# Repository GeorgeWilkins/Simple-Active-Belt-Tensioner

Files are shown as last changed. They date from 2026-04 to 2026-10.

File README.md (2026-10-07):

> 📢 **Important:** This is a _pre-release_ of the project and considered to be under active development and testing. If you're not prepared to do some tinkering and/or deal with initial usability issues, it is recommended that you do not attempt to build it right now and instead wait for the `v1.0` release

> 📰 **Latest News:** We now have a [Discord Server](https://discord.gg/YwW3TvEJEv) for pre-build questions, troubleshooting and technical support. You can also share details and photos of your build there!

SABT Logo

Diagram

# Simple Active Belt Tensioner

A haptic device for sim racing, designed specifically for people who do not have a background in software or electronics.

It requires **no soldering or programming** and can be built for **as little as ~215 GBP** _including the harness_.

## What Is It?

Introduction Video (https://youtu.be/b3R1tQvu-o4)

An _active belt tensioner_ is a device that attaches between your sim rig and the anchor points of your racing harness. It dynamically tensions the harness in response to game telemetry; giving a sense of the forces you'd be experencing in a vehicle when changing speed, braking, cornering and jumping/landing.

It works with **any game fully supported by [SimHub](https://www.simhubdash.com/)**, but the current software is designed primarily for racing games and simulators.

This project consists of three parts:
- A shopping list of [components](#what-does-it-cost), readily available from online sellers
- Printable [parts](/Printables/) and instructions on how to assemble them
- A _SimHub_ plugin that controls the hardware and allows customisation of the effects

The printable files and software are **completely free** (except the required [SimHub License](https://www.simhubdash.com/get-a-license/)). The printed part designs are `CERN-OHL-P` licensed (open-source), and the software is `MIT` licensed, which essentially means you can do what you like with either; including selling printed/machined parts kits.

### Design Goals
- Lowest Practical Cost
- Minimal Parts & Tools
- No Soldering
- No Programming
- No 'Reclaimed' Parts
- Direct-Drive (FOC/BLDC) Performance & Flexibility

## Who Is It For?

Anyone with a sim rig that desires a more immersive experience. It's a plug-and-play design that requires no soldering or programming, so virtually anyone can build it.

Note that you'll need either an _aluminium profile_ or _tubular steel_ sim rig frame to mount this using the available brackets. Mounting to other types of rig is possible, but you'll need to design and fabricate your own brackets (or [get in touch](mailto:sabt@georgewilkins.co.uk) with me).

I would recommend installing tactile transducers (bass shakers) before embarking on belt tensioners and other more exotic haptic systems. Transducers are by far the simplest and cheapest way of adding real immersion to your experience. They provide detail that belt tensioners cannot (road bumps, curbs, etc), while tensioners provide constant forces that transducers cannot (braking, cornering, etc).

### Community Builds
As of October 2026, at least _forty_ SABT builds are known to exist; probably many more.

Several members of the sim racing community have already provided photographs of their SABT builds, which I've added to a [shared album](https://photos.app.goo.gl/ju7rso1PFKGxnRhJ8); but we're moving over to a new [Discord Server](https://discord.gg/YwW3TvEJEv), where there is a dedicated channel allowing builders to post their builds directly.

## What Does It Cost?

If you have your own 3D printer, as little as **215 GBP** including taxes and delivery. If not, **250~300 GBP** depending on your choice of printed parts supplier.

### Purchased Parts
| Price (GBP) | Part | Notes |
| - | - | - |
| 120 | 2 x Motors | Provides the tensioning force |
| 20 | Controller | Provides USB control of the motors |
| 6 | 2 x Bearings | Allows the pulley covers to rotate smoothly |
| 7 | Screw & Nut Set | Provides every needed fastener in one set (with _many_ spares) |
| 5 | 1M Cord | A low-friction cord that winds around the pulleys (attached at the other end to your belts) |
| 20 | Power Supply | Provides DC power to the motors |
| 12 | Back Driving Protection Unit | Prevents power-supply resets if the motors are back-driven (**optional but recommended**) |
| 25 | 4/5/6-Point 2" Harness | A low-cost Aliexpress model or used/expired FIA harness |
| **215** | **Total** | ...excluding printables |

There is a [detailed parts list](/INSTRUCTIONS.md#motors-electronics--fixings) with sources in the build guide.

### Printing Options
| Price (GBP) | Method | Notes |
| - | - | - |
| 5~10 | Self-Print | Roughly 200g or 75M of filament |
| 30~60 | FDM Service | Assuming an _eBay-tier_ printing provider, not a professional company |
| 60~90 | MJF/SLS Service | [JLC3DP](http://jlc3dp.com/) and [3DPrintUK](http://3dprint-uk.co.uk/) used for reference pricing (nylon dyed black with peening) |

### Other Costs
Note that you will also need [SimHub Licensed Edition](https://www.simhubdash.com/get-a-license/) (currently **8 EUR** or more) to use this device. If you're reading this, you almost certainly already have it.

## How Does It Work?

The two motors are anchored to your rig with printed brackets. A self-orienting pulley is attached to the face of each motor.

The ends of each shoulder belt are attached to lengths UHMWPE/Dyneema cord, which are wrapped around each motor pulley.

When SimHub sends game telemetry to our plugin, it converts this into torque commands and send them to the motors over a serial connection.

## How Does It Perform?

Since we're using high-quality BLDC/FOC integrated servo motors, the effects are applied directly as _force_ (torque) rather than emulated by moving the belts a fixed distance, as with some DIY tensioners based on RC servos.

The benefits of this are:
- Smooth and silent operation
- Compact & clean design
- Auto-adjusting of the harness (adjustable idle tension)

The maximum force appliable by these motors with the current pulley design is about **10Kgf per belt**, putting us right around the rated mechanical loading for each motor. Imagine having **~10Kg of weights** attached to each belt hanging down from the back of your seat, and you'll get the idea.

This is plenty to give extra immersion and feedback, but significantly less than you'd feel in a real vehicle at motorsport velocities.

For comparison, the [QS-BT1](https://qubicsystem.com/product/qs-bt1) claims _"20.5kg per channel"_, but is a considerably larger and costs six times more.

Note that this system conveys progressive constant forces (cornering, braking, etc) rather than fine details (road texture, track kerbs, etc). For the latter, you should install one or more tactile transducers. The two work together to imply the sensation of movement without a costly motion simulator.

[Force Testing.webm](https://github.com/user-attachments/assets/be7b9d7a-be3f-46f7-abf1-9659297854bb)

## Anything I Should Be Aware Of?

There is considerable variation in rig, seat and harness designs, so I cannot anticipate every possible configuration. You'll need to decide if this system is suitable for your rig by looking at the installations examples and instructions.

Of particular note:
- The belt clamp designs are intended for 2" wide belts of up to 2MM thickness. If your belts are wider or thicker than this, you will need to modify the design (or let me know and I'll create additional designs)
- The need for belt rollers depends on the seat design. In many cases applying low-friction tape is sufficient. A 'universal' [Belt Roller](INSTRUCTIONS.md#belt-rollers) design is included should you wish to use it
- The system includes a design for a [Back Driving Protection Unit](INSTRUCTIONS.md#back-driving-protection), which prevents your power supply's protection circuitry from tripping when the motors are back-driven (e.g. by pulling fast on the belts). This is an optional component, but highly recommended. A _zero-soldering solution_ is available, but even the soldered version is very simple to assemble
- Although the motors and driver board can tolerate up to `24V`, I've found that `15V` works just fine. Common `19V~20V` laptop power supplies are used by many SABT builders without issue; but using anything higher risks damage to the motors under back-driving conditions (pulling aggressively on the belts)

## Is It Safe?

This is an open-source project involving powerful motors, pinch points and moving belts attached to your body.

⚠️ **No claims are made regarding the safety of this device. You are responsible for ensuring its safe use and no liability is accepted by the creator(s) for any damage or injury caused by this device.**

With that said, design measures have been taken with safety in mind. See [SAFETY.md](SAFETY.md) for details.

## How Do I Get Started?

Read through the [instructions](/INSTRUCTIONS.md) to get a better idea of what's involved and how to proceed.

> 📢 **Important:** This is a _pre-release_ of the project and considered to be under active development and testing. If you're not prepared to do some tinkering and/or deal with initial usability issues, it is recommended that you do not attempt to build it right now and instead wait for the `v1.0` release

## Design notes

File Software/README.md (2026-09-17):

# Software

There are two things you'll need to use this belt tensioner:
- [SimHub](https://www.simhubdash.com/) and a [License](https://www.simhubdash.com/get-a-license/) for 60FPS telemetry data
- The project's SimHub plugin, which must be copied into SimHub's installation directory

## Downloading SimHub

SimHub is going to already be on your machine or at least familiar to you if you have a sim rig. In case it's not, it's a popular utility in the Sim Racing community that collates and normalises telemtery data from various games and simulators, making it available to many devices and plugins. Our tensioner uses that telemetry to determine how much tension to apply to the belt at any given moment.

1. Go to [https://www.simhubdash.com/](https://www.simhubdash.com/) and click on `Download now` or the `Download` link at the top of the page
2. You'll see a large button, labelled something like `Download SimHub vX.X.X`, which will start the download when clicked
3. Unzip the downloaded file and run the executable within to install SimHub on your computer
4. Run SimHub at least once before attempting to install the plugin

## Licensing Simhub

The free version of SimHub offers 10Hz telemetry updates, which is sufficient for some devicces; but not for our tensioner. We'll need to buy a license to unlock 60Hz updates. It's cheap (as little as 8 EUR for a perpetual license) and absolutely worth the money.

Note that you do not need a _'Motion License'_ to use this tensioner; that is a more costly thing for full motion rigs. The regular license is sufficient for our needs.

1. Go to [https://www.simhubdash.com/](https://www.simhubdash.com/) and click on the `Get a license` link at the top of the page
2. Enter your details and complete payment
3. Grab the key from the e-mail you're sent and enter it into `Settings` > `General` > `Licenses` within SimHub
4. Once done you should see `Status: Licensed` at the bottom of the SimHub window

## Downloading & Installing The Plugin

1. Make sure _SimHub_ is closed before proceeding
2. Download the latest [SABT SimHub Plugin.zip](https://github.com/GeorgeWilkins/Simple-Active-Belt-Tensioner/releases/latest/download/SABT.SimHub.Plugin.zip)
3. Unzip the downloaded file, which will contain a `.dll` file (the plugin itself) and a `/Languages/` folder
3. Copy both into your SimHub installation directory (e.g. `C:\Program Files\SimHub`)
4. Open _SimHub_, which should then recognise the plugin and load it
5. Click on the `Simple Active Belt Tensioner` plugin in the left-hand menu and configure it as you like

You can change the language of the plugin (and SimHub itself) from `Settings` > `General` > `Language`.

## Configuring The Plugin
The plugin contains instructions on how to initially set up the motors; a one-time process that uniquely identifies each motor so the plugin can send commands to each motor separately.

Beyond that, everything is documented within the plugin; including descriptions of the various sliders and options that control how the effects are applied.

SABT Plugin

### 📢 Important
_SimHub_ has an optional feature called _"Arduino"_, which may or may not be enabled in your installation. It is _completely unrelated to SABT_ and **not required** for SABT to work.

However if it is enabled, there is a good chance it will interfere with SABT by taking over the serial port presented by our motor controller.

You can check if it is enabled by clicking on `Add/remove features` within _SimHub_ and seeing if it is listed as an enabled plugin. Is it is, make sure `Show in left main menu` is toggled on, then find the `Arduino` menu item on the left-hand menu and open it.
 
To prevent it from causing problems, you can tell the _"Arduino"_ feature to stop scanning the SABT serial port, under the `ARDUINO SCAN SETTINGS` section as shown below.

Select the `Never scan selected ports` and toggle the numbered port that is labelled as `USB-Enhanced-SERIAL CH343`:

Arduino Feature

Once you've done this, unplug the SABT controller's USB cable, close _SimHub_ and then reopen it; finally plugging back in the USB cable. Our plugin should then be able to see and communicate with the motor controller.

Unfortunately _SimHub_ plugins and features can cause conflicts with each other, including SABT. If you've tried the steps above and are still having communication issues, have a look a the [FAQ.md](FAQ.md) document and finally reach out via [a new discussion](/discussions/new/choose) or [create a new issue](/issues/new), describing your problem and including _SimHub_ logs.

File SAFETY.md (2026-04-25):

# Safety

This is an open-source project involving powerful motors and moving belts attached to your body.

⚠️ **No claims are made regarding the safety of this device. You are responsible for ensuring its safe use and no liability is accepted by the creator(s) for any damage or injury caused by this device.**

With that said, certain measures have been taken with safety in mind:
- The motor pulley covers are designed to avoid fingers (or other appendages) from getting caught in the moving parts; though care should be taken not to touch the motors or cords while powered
- The maximum force applied is estimated to be around 8Kgf to 12Kgf per belt, which is unlikely to harm a healthy adult unless the system is installed and/or used improperly
- The motors are ungeared, meaning they have zero holding torque when unpowered; so a properly implemented emergency stop will immediately remove all force from the belts
- The SimHub pluging software has a few features intended to prevent unexpected motor action; though bugs are almost certainly present and this cannot be guaranteed

## Operational Safety
The same rules and guidance that apply to _any_ motion system apply here:
- **NEVER** touch the motors during or immediately after use; they may be hot to the touch
- **NEVER** touch the cords while powered; they may cause friction burns or trap appendages
- **NEVER** position your belts such that they might pinch, compress or catch your neck or head
- **NEVER** attach any sharp or protuding objects to your harness or belts
- **ALWAYS** keep children and pets away from the system while in use
- **ALWAYS** have an easily accessible emergency stop button or mechanism that cuts all power to the system **within easy reach while seated and strapped into the harness at full tension**
- **ALWAYS** disconnect or switch off the power supply to this device when not in use. Do not leave it powered indefinitely

## Mechanical Safety
- All fittings and fixtures must be fully tightened and secured, and checked regularly for signs of wear, damage or loosening
- Check your belts, cords and seat loops for wear regularly, and replace immediately if any signs of damage are found
- Check your printed parts regularly for signs of failure; layer separation, cracking or deformation. If any of these are found, stop using the system immediately and replace the affected parts before resuming use

## Electrical Safety
- Make sure the control box and all wiring is properly insulated and protected from accidental contact, shorting and damage. Ensure the box is securely mounted to the rig and cannot come loose while in use
- If you have installed the [Back Driving Protection Unit](INSTRUCTIONS.md#back-driving-protection), make sure it is inserted correctly, protected from external shorting and secured in place so it cannot come loose. Ensure you do not touch the terminals of the unit while powered or after use, as the capacitor within will hold a charge even after diconnection from a power source
- Ensure your cables, sockets and fuses are rated appropriately for the total rated draw of the connected devices

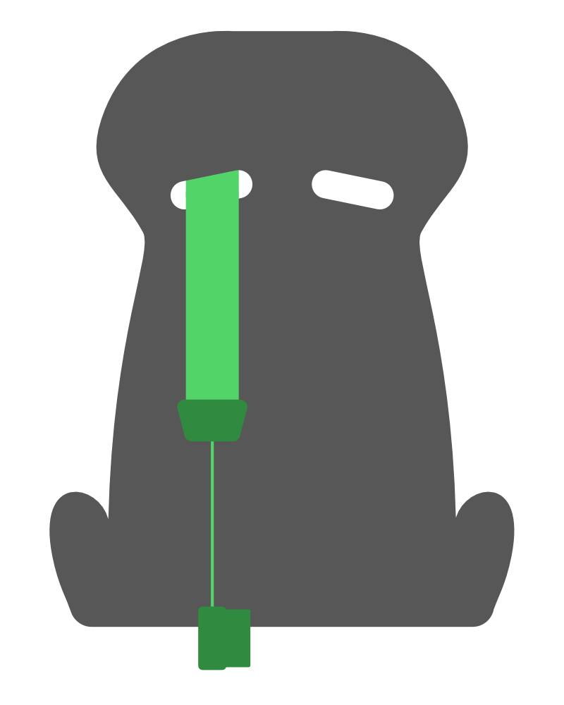
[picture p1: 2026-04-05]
Sources/Plugin/Motor.png

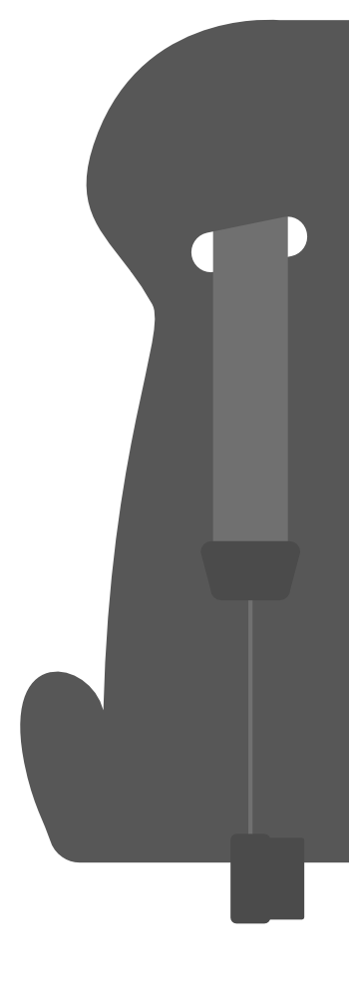
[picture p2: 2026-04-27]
Sources/Plugin/Motor, Disconnected.png

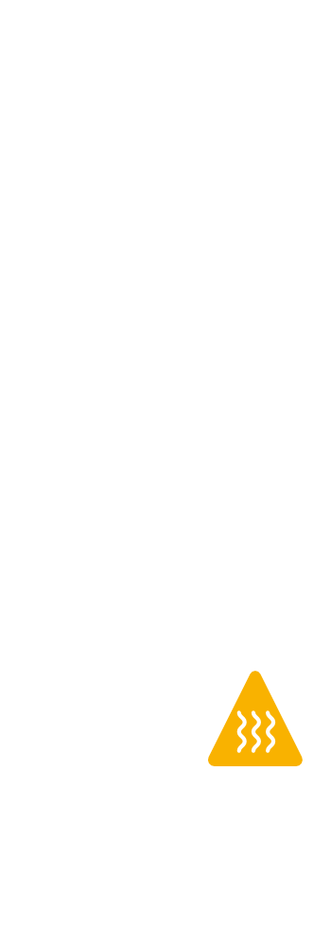
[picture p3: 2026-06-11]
Sources/Plugin/Motor, Overheating.png

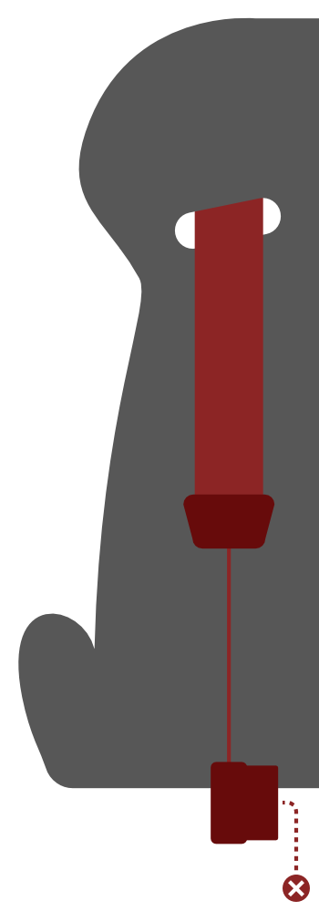
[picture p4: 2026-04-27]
Sources/Plugin/Motor, Error.png

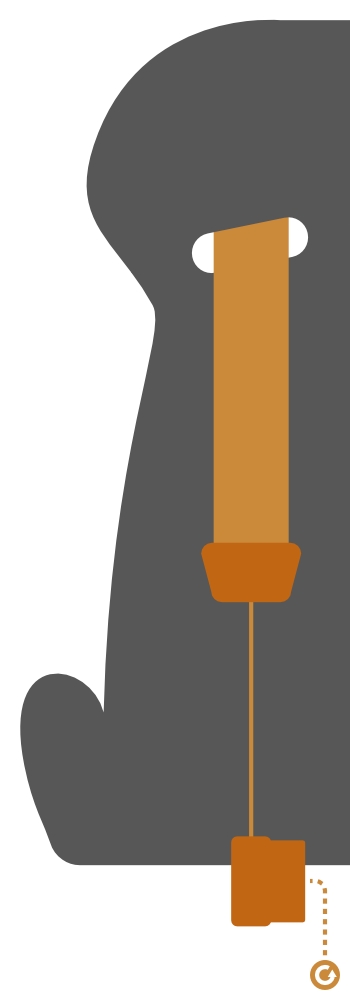
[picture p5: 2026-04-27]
Sources/Plugin/Motor, Communicating.png

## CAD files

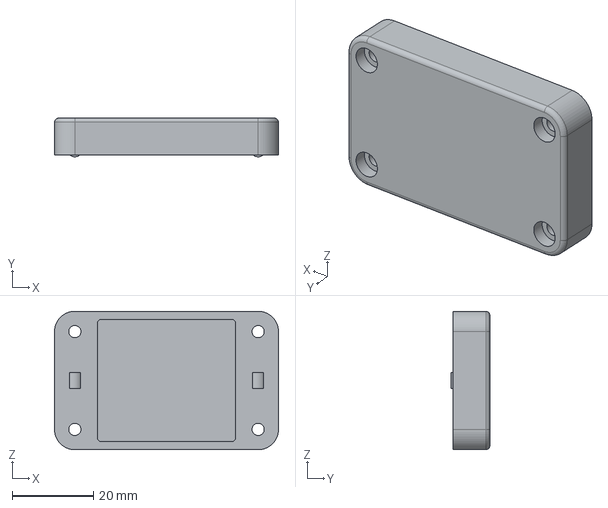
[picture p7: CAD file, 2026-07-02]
Printables/Back-Driving Protection Case/Top.step
55.0 x 9.50 x 34.0 mm

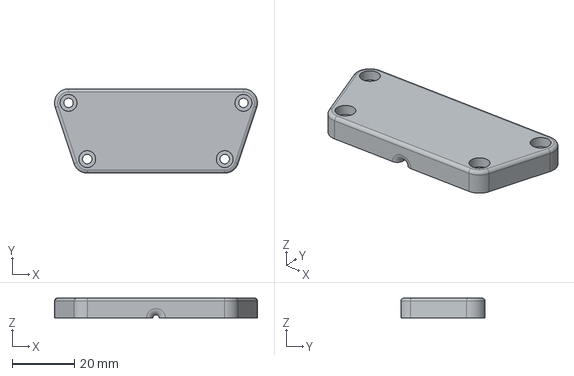
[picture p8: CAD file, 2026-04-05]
Printables/Belt Clamps/For Belt Ends/Front.step
65.0 x 27.0 x 6.40 mm

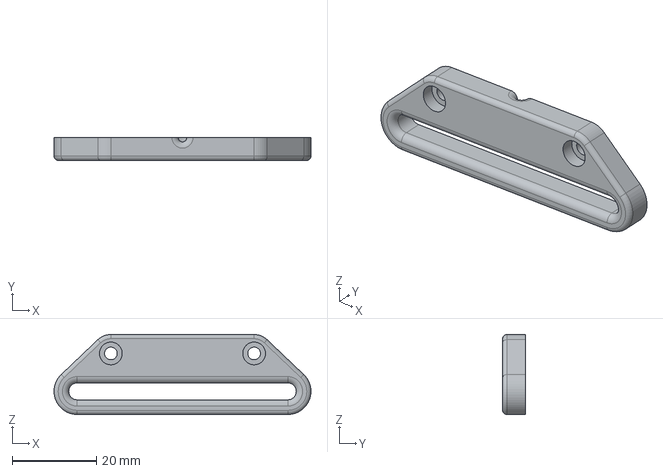
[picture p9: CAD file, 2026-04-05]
Printables/Belt Clamps/For Belt Loops/Front.step
61.0 x 5.40 x 19.0 mm

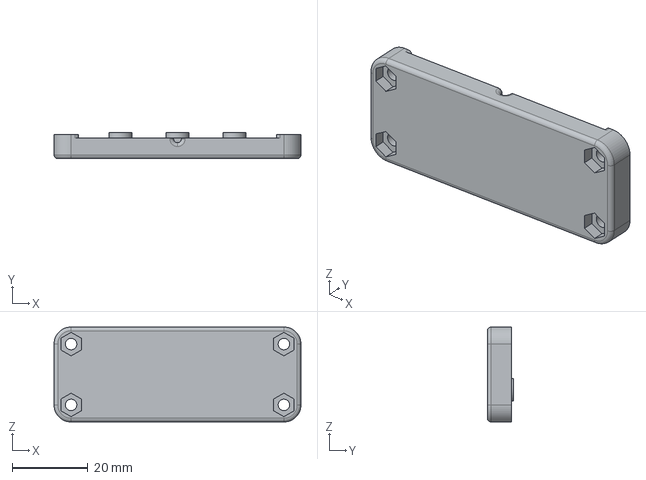
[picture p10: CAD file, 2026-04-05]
Printables/Belt Clamps/For Belt Passthrough/Rear.step
65.0 x 6.90 x 25.0 mm

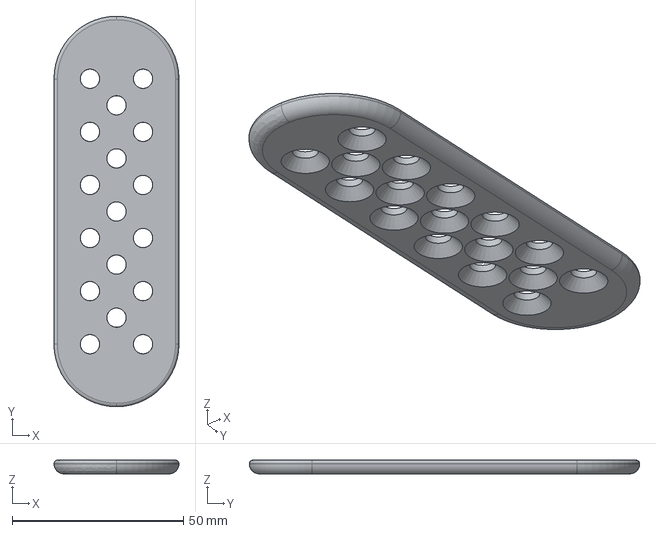
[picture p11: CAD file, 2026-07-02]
Printables/Belt Rollers/Plate.step
36.5 x 114.0 x 4.00 mm

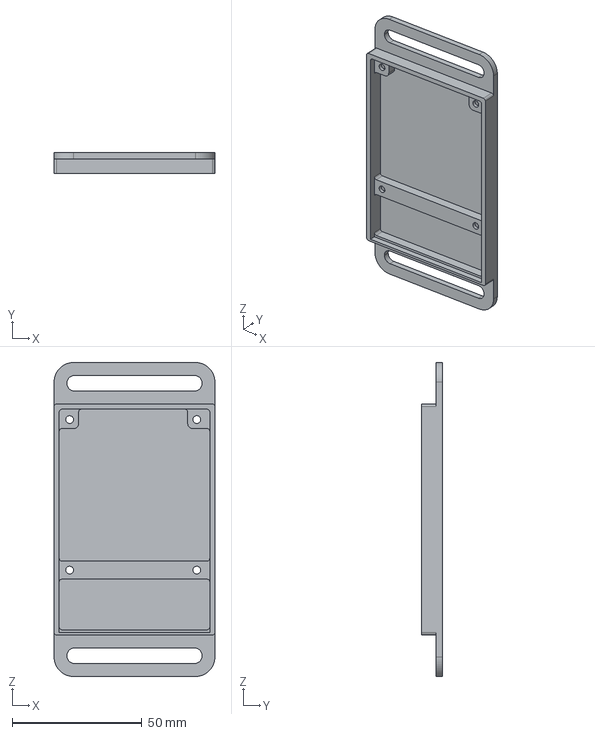
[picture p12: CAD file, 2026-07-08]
Printables/Controller Case/Base (With End Tabs).step
62.0 x 8.00 x 121.0 mm

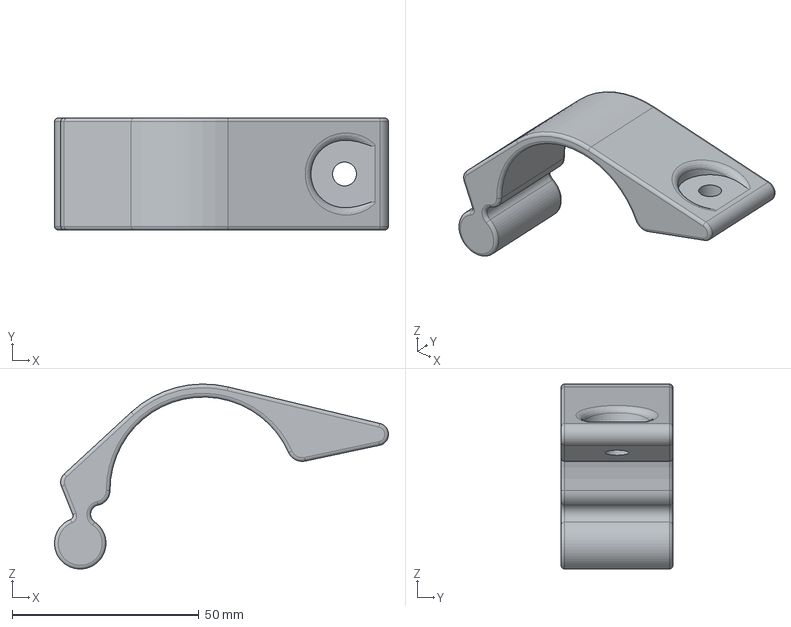
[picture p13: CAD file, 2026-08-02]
Printables/Motor Brackets/For 2-Inch Tube/Clamp.step
89.5 x 30.0 x 49.6 mm

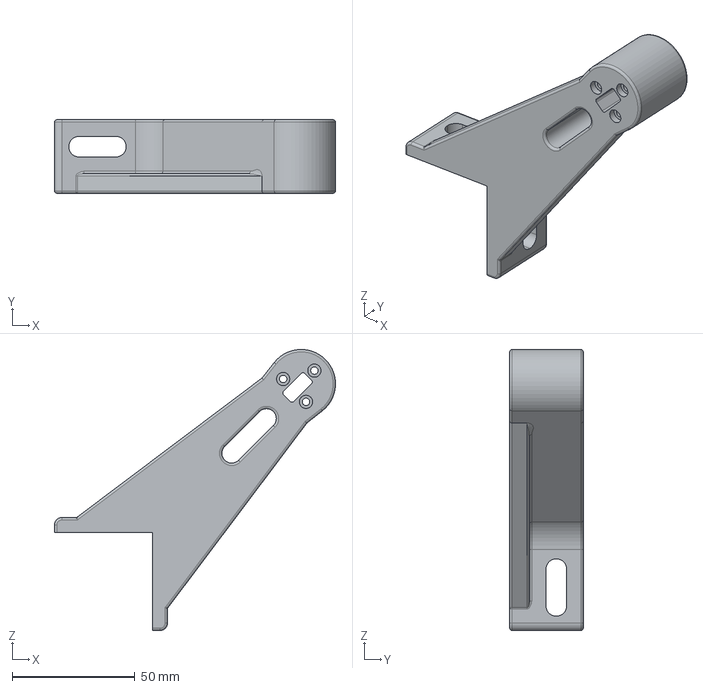
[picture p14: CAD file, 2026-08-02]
Printables/Motor Brackets/For Aluminium Profile Edge (15~20mm Hole Inset)/Bracket (Tall).step
114.4 x 30.0 x 114.4 mm

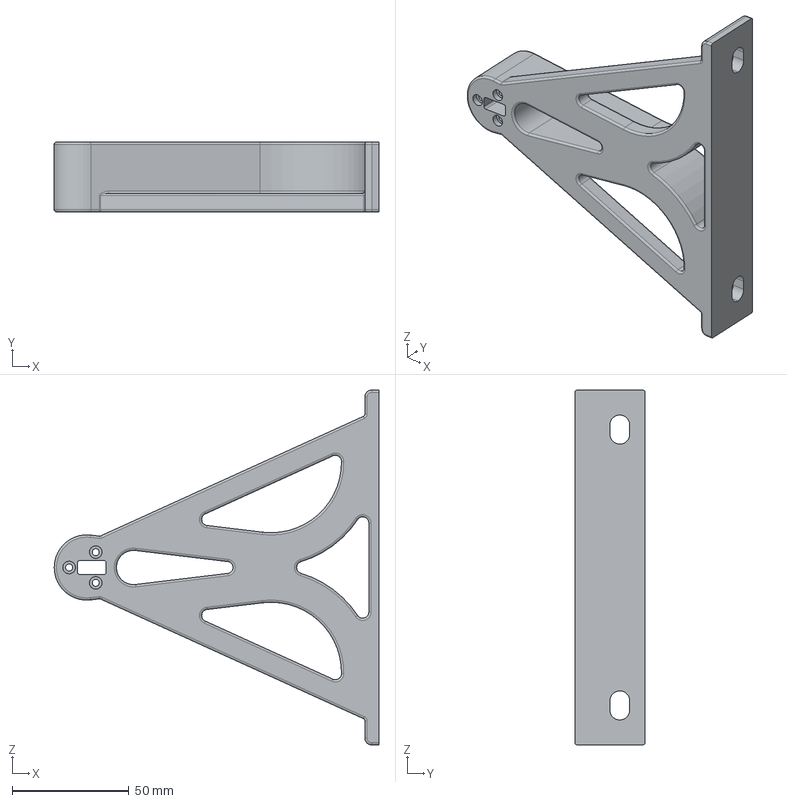
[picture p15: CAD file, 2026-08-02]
Printables/Motor Brackets/For Aluminium Profile Face (120mm Hole Spacing)/Bracket (Tall).step
139.0 x 30.0 x 152.0 mm

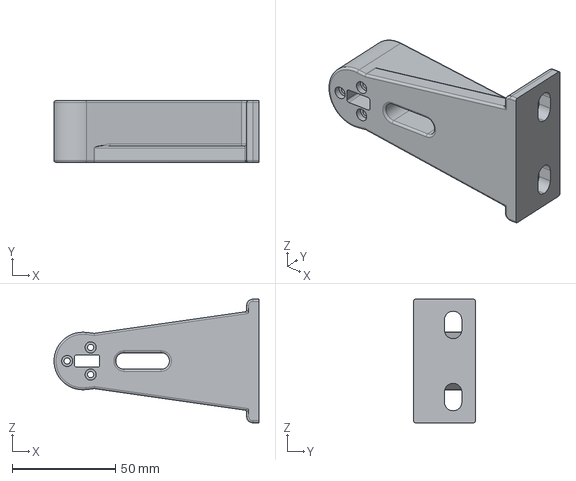
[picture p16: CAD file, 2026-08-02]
Printables/Motor Brackets/For Aluminium Profile Face (30~40mm Hole Spacing)/Bracket (Tall).step
99.5 x 30.0 x 60.0 mm

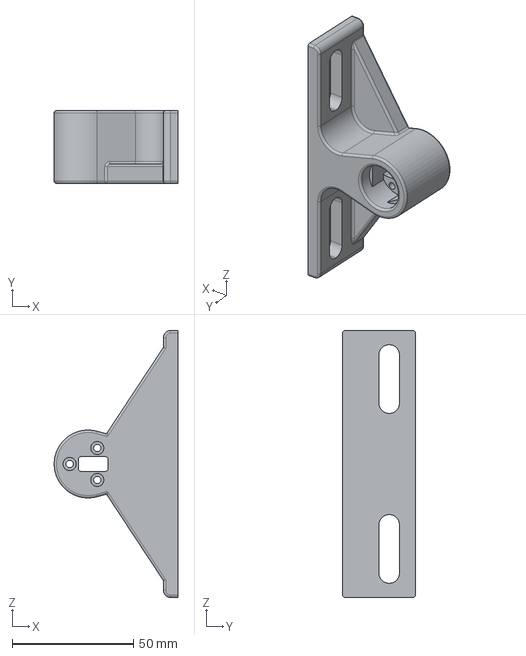
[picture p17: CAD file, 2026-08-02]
Printables/Motor Brackets/For Aluminium Profile Face (50~90mm Hole Spacing)/Bracket (Short).step
51.0 x 30.0 x 110.0 mm

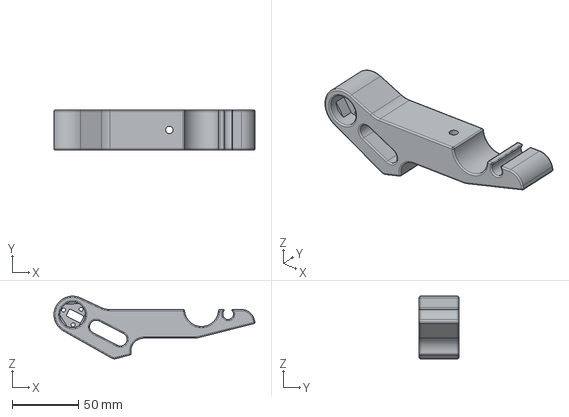
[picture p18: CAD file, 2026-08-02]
Printables/Motor Brackets/For Playseat Challenge/Bracket.step
151.2 x 30.0 x 47.2 mm

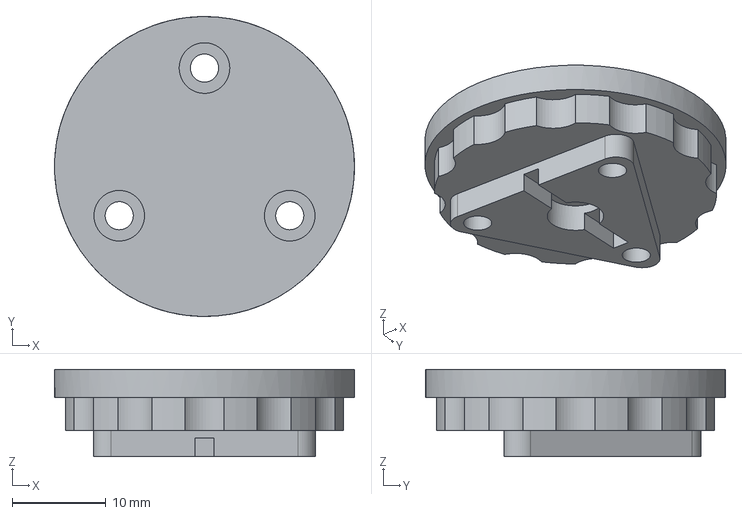
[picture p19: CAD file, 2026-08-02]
Printables/Pulleys/Face.step
32.0 x 32.0 x 9.30 mm

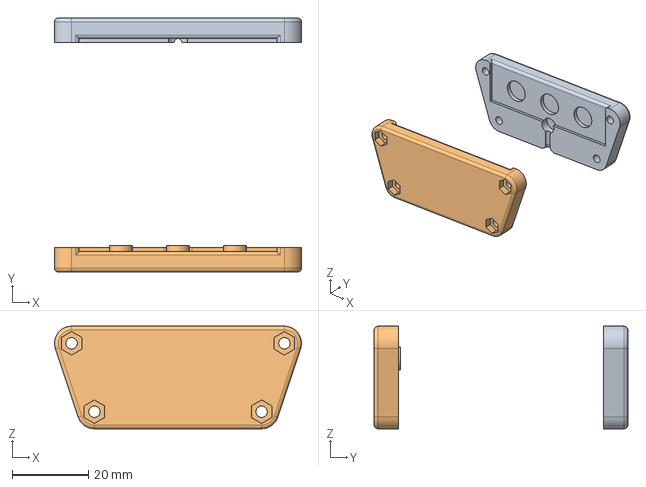
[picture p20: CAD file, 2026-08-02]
Sources/Printables/Belt Clamps/For Belt Ends.FCStd
65.0 x 66.8 x 27.0 mm
Front
Back

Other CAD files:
Sources/Printables/Motor Brackets/For Aluminium Profile Face (30~40mm Hole Spacing, Short).FCStd
Sources/Printables/Pulleys.FCStd
Printables/Back-Driving Protection Case/Base.step
Printables/Belt Clamps/For Belt Ends/Rear.step
Printables/Belt Clamps/For Belt Loops/Rear.step
Printables/Belt Clamps/For Belt Passthrough/Front.step
Printables/Belt Rollers/Bracket.step
Printables/Belt Rollers/Roller.step
Printables/Belt Rollers/Spacer.step
Printables/Controller Case/Base (With Side Tabs).step
Printables/Controller Case/Controller Case (Base).step
Printables/Controller Case/Top.step
Printables/Motor Brackets/For 2-Inch Tube/Bracket.step
Printables/Motor Brackets/For Aluminium Profile Edge (15~20mm Hole Inset)/Bracket (Short).step
Printables/Motor Brackets/For Aluminium Profile Face (30~40mm Hole Spacing)/Bracket (Short).step
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

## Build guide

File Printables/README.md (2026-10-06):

 # Printables

The files in this directory and its sub-directories are what you need to print (or to have printed by a third party) to complete the kit.

Since there are a couple of options to choose from, you should read this before selecting and printing (or ordering) your parts.

### Choosing Your Brackets

Flat Motor Bracket (30~40mm Hole Spacing)

There are two main types of sim rig frame:
- **Profile / Extrusion** (e.g. [GT Omega Prime](https://www.gtomega.co.uk/products/prime-cockpit)) typically use `40-Series` aluminium extrusion that is bolted together in a modular fashion
- **Tubular** (e.g. [GT Omega Titan](https://www.gtomega.co.uk/products/titan-cockpit)) typically use `2"` steel tubing that is mandrel-bent into shape and welded together. Lighter foldable frames may use `1"` tubing instead

If you have a **profile frame**, choose from the `For Aluminium Profile...` bracket designs; selecting from `Edge` or `Face` mounting options with the appropriate hole spacing for your particular size of aluminium profile. If you're uncertain, load them up into your preferred slicer and use the measuring tool to check the dimensions.

Most bracket options have `Short` and `Tall` variants to choose from. Use the latter only if you need additional clearance.

If you have a **tubular frame**, choose from the `For {Size} Tube...` bracket designs.

Alternatively there may be a _brand-specific_ bracket design available for your frame, where non-standard fitment is required.

You only need to print _two_ of a single type of bracket; though some designs have multiple parts (the tube clamps in particular). Many bracket designs are symmetrical, _but not all_. Non-symmertical designs require one of the printed brackets to be mirrored in your slicer, so check this before printing.

Here are the various bracket options plated up in a slicer so you can see the intended printing orientations:

Bracket Designs

### Choosing Your Belt Clamps

Since there are a variety of belt types and terminations, a few options are available:
- [For Belt Ends](/Printables/Belt%20Clamps/For%20Belt%20Ends/): This is designed to clamp the plain end of an unterminated 2" belt (suitable for bare belt ends, or belts you are happy to shorten to the ideal length)
- [For Belt Loops](/Printables/Belt%20Clamps/For%20Belt%20Loops/): This is designed to loop through a 2" belt (up to 4mm thick) and secure back on itself using a standard belt buckle (likely to have come with your hanress)
- [For Belt Passthrough](/Printables/Belt%20Clamps/For%20Belt%20Passthrough/): This is designed to clamp anywhere along a 2" belt without needing to shorten or terminate the belt itself

The [Belt Passthrough](/Printables/Belt%20Clamps/For%20Belt%20Passthrough/) option is probably the easiest to integrate, while the [Belt Ends](/Printables/Belt%20Clamps/For%20Belt%20Ends/) option is the neatest; but needing the belts to be shortened specifically for the tensioner (or shortened non-destructively with buckles).

Here are the various clamp options plated up in a slicer so you can see the intended printing orientations:

Clamp Designs

### Opting For Belt Rollers

There's a lot of variation in seat design. In cases where the belt guides have horizontal bottom surfaces (perpendicular to your pulley cords), you don't _need_ belt rollers; the belts will just slide through the guides without issue. In this case low-friction tape _is_ recommended for a smoother experience and to protect your belt guides.

However with irregular or angled belt guides, you may run into issues with the belts bunching up in the corners of the guides and not sliding smoothly. For such cases, you can print and assemble two 'universal' [belt rollers](/Printables/Belt%20Roller/), which have been designed with an array of mounting holes to accommodate most belt guide shapes and angles.

These will not work well with curved belt guides (where they match the curvature of the seat). In such cases you may need to design your own version of the roller. You can use the [FreeCAD source file](/Sources/Printables/Belt%20Roller.FCStd) as a reference and starting point if so.

## Printables List

Regardless of your choices above, you should end up with:
- 2x Belt Clamps > For Belt `Ends`|`Loops`|`Passthrough` > **Front**
- 2x Belt Clamps > For Belt `Ends`|`Loops`|`Passthrough` > **Rear**
- 1x Controller Case > **Base** With `Side`|`End` Tabs
- 1x Controller Case > **Top**
- 2x Motor Brackets > _Parts Vary_
- 2x Pulleys > **Cover**
- 2x Pulleys > **Face**
- 2x Pulleys > **Hub**

If you're making the [Back-Driving Protection Unit](/INSTRUCTIONS.md#back-driving-protection) you'll additionally need:
- 1x Back-Driving Protection Case > **Base**
- 1x Back-Driving Protection Case > **Top**

If you're making the [Belt Rollers](/Belt%20Rollers) you'll additionally need:
- 2x Belt Rollers > **Bracket**
- 2x Belt Rollers > **Plate**
- 2x Belt Rollers > **Roller**
- 4~8x Belt Rollers > **Spacer** \*

\* These are intended to be vertically scaled in your slicer software to be slightly shorter (by `~0.5mm`) than the depth of your belt guide (usually `12~40mm`). They help to prevent the bracket and plate from bending once clamped and also protect your belt guide plastics from the screw threads. It is recommended that you print the rollers and spacers together (in a vertical orientation) and the bracket and plate together (in a horizontal orientation).

### Self Printing

Obviously if you have your own 3D printer, you can print these yourself. These parts have been designed with hobby FDM printers in mind (not SLA/DLP/MSLA/LCD resin printers).

All parts have been designed to avoid overhangs where possible, making them printable without supports. The only exceptions are parts with counterbored bolt & nut holes, which may need supports depending on how well-tuned your printer is and the selected slicing settings.

The default orientation of the STEP files likely won't be appropriate when imported into your slicer; so use the auto-orient feature or manually rotate the parts to be flat on the print bed. The preferred orientation will be obvious from the geometry of the parts.

I've used [DEEPLE PLA Plus](https://www.amazon.co.uk/dp/B0F66H47J8) on my Bambu H2S for all of my own prints; but virtually _any_ strong PLA/ABS/PETG filament should be fine. Fibre-reinforced filament is okay for the mounting brackets but _not reccommended_ for the pulley parts due to abrasion concerns.

If you're able to, printing in a more heat-resistant filament such as ABS or PETG is preferred over PLA. The motors are capable of operating at _much_ higher temperatures than PLA can cope with; but under normal operation they should not get warm enough to pose a problem. The **SABT** plugin has thermal controls that allow you to reduce the motor output if the temperatures reach a threshold you set; so whatever you print in, you can adjust that to match your material.

As for printing settings, I would suggest:
| Setting | Value |
| - | - |
| Layer Height | `0.16` |
| Walls | `7` |
| Top Shell Layers | `7` |
| Bottom Shell Layers | `7` |
| Infill Density | `30%` |
| Supports | `Manual` |

Manually add supports to the counterbored bolt & nut holes _only_. They aren't needed anywhere else.

The above takes about **8 hours** on my H2S if printing everything at once. It uses about 75M of filament, or ~230g of filament. I'd suggest you do the parts in smaller batchces though, to minimise wastage if something goes wrong during the print.

### Third-Party Printing

There are plenty of hobbyists on eBay offering low-cost FDM printing. Quality will depend very much on the individual seller.

If you want a more commercial-looking end result, there are companies running SLS/MJF machines which produce Nylon parts for reasonable money:
- [3DPrintUK](https://3dprint-uk.co.uk) are a provider of SLS/MJF Nylon parts in the UK. They have an instant quotation system that will give you a price right away (~**90 GBP** at the time of writing)
- [JLC3DP](https://jlc3dp.com) offer a similar service out of China with delivery to most countries

I've had test prints done in MJF Nylon PA12 (dyed black & shot peened) which came out great, but as with FDM printing, getting the tolerances correct for the press-fit bearings requires some trial and error.

FDM PLA (Left) &amp; MJF Nylon (Right)
FDM PLA (Left) &amp; MJF Nylon (Right)

### CNC Machining

At some point I'd love to see machined aluminium parts become available; but the parts included in this repository are very much designed for FDM printing, not CNC subtractive manufacturing.

Some of the parts would need to be adapted considerably to work with the latter process.

If you have the means to do this and want to make them available, please get in touch.

## Downloading

The printable files are provided in the `STEP` format. This provides the highest quality of geometry while being compatible with all major 3D printer slicing sofware _and_ commercial printing and CNC services.

GitHub treats these as _text_ files, so displays their contents rather than offering a download. To download a printable `STEP` file, use the `Download Raw File` option, which looks like a _tray and arrow_ icon:
Download STEP File

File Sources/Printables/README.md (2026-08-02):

# FreeCAD Source Files

If you're here looking for things to print, _you're in the wrong place_; go [here](/Printables) instead.

These files are the original [FreeCAD](https://www.freecad.org/) design files from which the printable `.STEP` files are generated. You'll only need these if you intend to change the designs of the parts.

| File | Part | Description |
| - | - | - |
| [Controller Case.FCStd](Controller%20Case.FCStd) | Electronics Case | The two halves of the **controller case** (including two mounting variations of the base) |
| [Back-Driving Protection Case.FCStd](Back-Driving%20Protection%20Case.FCStd) | Electronics Case | The two halves of the **back-driving protection unit case** |
| [Belt Rollers.FCStd](Belt%20Rollers.FCStd) | Belt Roller | The **belt roller** assembly |
| [Belt Clamps > For Belt Ends.FCStd](Belt%20Clamps/For%20Belt%20Ends.FCStd) | Belt Clamp | The two halves of a **belt clamp** (suitable for clamping the plain end of a 2" belt) |
| [Belt Clamps > For Belt Loops.FCStd](Belt%20Clamps/For%20Belt%20Loops.FCStd) | Belt Clamp | The two halves of a **belt clamp** (suitable for looping through a 2" belt) |
| [Belt Clamps > For Belt Passthrough.FCStd](Belt%20Clamps/For%20Belt%20Passthrough.FCStd) | Belt Clamp | The two halves of a **belt clamp** (suitable for clamping anywhere along a 2" belt) |
| [Motor Brackets > For Aluminium Profile Edge (15~20mm Hole Inset), Short).FCStd](Motor%20Brackets/For%20Aluminium%20Profile%20Edge%20(15~20mm%20Hole%20Inset)%20Short.FCStd) | Motor Bracket | A motor bracket designed to be **edge-mounted** to `30MM` or `40MM` aluminium profile |
| [Motor Brackets > For Aluminium Profile Edge (15~30mm Hole Inset), Tall).FCStd](Motor%20Brackets/For%20Aluminium%20Profile%20Edge%20(15~30mm%20Hole%20Inset),%20Tall.FCStd) | Motor Bracket | A motor bracket designed to be **edge-mounted** to `30MM` or `40MM` aluminium profile, with an additional `50mm` of motor distance from the mounting surface |
| [Motor Brackets > For Aluminium Profile Face (30~40mm Hole Spacing, Short).FCStd](Motor%20Brackets/For%20Aluminium%20Profile%20Face%20(30~40mm%20Hole%20Spacing,%20Short).FCStd) | Motor Bracket | A motor bracket designed to be **face-mounted** to `30MM` or `40MM` aluminium profile |
| [Motor Brackets > For Aluminium Profile Face (30~40mm Hole Spacing, Tall).FCStd](Motor%20Brackets/For%20Aluminium%20Profile%20Face%20(30~40mm%20Hole%20Spacing),%20Tall.FCStd) | Motor Bracket | A motor bracket designed to be **face-mounted** to `30MM` or `40MM` aluminium profile, with an additional `50mm` of motor distance from the mounting surface |
| [Motor Brackets > For Aluminium Profile Face (50~90mm Hole Spacing, Short).FCStd](Motor%20Brackets/For%20Aluminium%20Profile%20Face%20(50~90mm%20Hole%20Spacing,%20Short).FCStd) | Motor Bracket | A motor bracket designed to be **face-mounted** to larger or more unusual aluminium profiles |
| [Motor Brackets > For Aluminium Profile Face (50~90mm Hole Spacing, Tall).FCStd](Motor%20Brackets/For%20Aluminium%20Profile%20Face%20(50~90mm%20Hole%20Spacing,%20Tall).FCStd) | Motor Bracket | A motor bracket designed to be **face-mounted** to larger or more unusual aluminium profiles, with an additional `50mm` of motor distance from the mounting surface |
| [Motor Brackets > For Aluminium Profile Face (120mm Hole Spacing, Tall).FCStd](Motor%20Brackets/For%20Aluminium%20Profile%20Face%20(120mm%20Hole%20Spacing,%20Tall).FCStd) | Motor Bracket | A motor bracket designed to be **face-mounted** to unusual aluminium profiles |
| [Motor Brackets > For 2-Inch Tube.FCStd](Motor%20Brackets/For%202-Inch%20Tube.FCStd) | Motor Bracket | A motor bracket designed to be **clamp-mounted** to `2"` tube |
| [Motor Brackets > For Playseat Challenge.FCStd](Motor%20Brackets/For%20Playseat%20Challenge.FCStd) | Motor Bracket | A motor bracket designed specifically for the [Playseat Challenge](https://www.playseat.com/en-gb/products/playseat-challenge-actifit) (experimental) |
| [Pulleys.FCStd](Pulleys.FCStd) | Pulley Assembly | The **pulley** cover, hub and face parts |

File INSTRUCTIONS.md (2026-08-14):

# Instructions

Everything you need to know about building a tensioner of your own is in this document. Please make sure you at least skim through each section before proceeding.

## Printed Parts

See the [/Printables/](/Printables/) directory to obtain the printable files, and detailed information on printing them. Make sure you read through this document and note which printable parts you _actually need_.

## Ordering Components
### Motors, Electronics & Fixings

You should be able to order the _Waveshare_ [motors](https://www.waveshare.com/wiki/DDSM115) and [control board](http://www.waveshare.com/wiki/DDSM_Driver_HAT_(A)) from the same supplier, as they are almost always stocked together. They are designed for robotics projects, so those kinds of retailers are your best bet.

The rest of the parts can be obtained from virtually anywhere, including [Amazon](https://www.amazon.co.uk) or [AliExpress](https://www.aliexpress.com). Where I've linked to particular products, these are not endorsements or items I've tested; simply representative examples. Shop around, as prices change constantly...

| Guide Price | Part | Description | Example |
| - | - | - | - |
| `60 GBP` `x2` | 2 x `DDSM115` _or_ `M0601` Motors | Waveshare or DFRobot servo motors | [PiHut UK](https://thepihut.com/products/ddsm115-direct-drive-servo-motor) / [Waveshare](https://www.waveshare.com/ddsm115.htm) / [DFRobot](https://www.dfrobot.com/product-3077.html) |
| `20 GBP` | `DDSM Driver HAT (A)` | Waveshare Controller Board (Version `A`) | [PiHut UK](https://thepihut.com/products/ddsm-hub-motor-driver-board) |
| `6 GBP` | 2 x `6706` Bearings | `30x37x4mm` bearings for the pulleys | [Amazon UK](https://www.amazon.co.uk/dp/B0D4DN3RW8) |
| `7 GBP` | `M2.5` Screw & Nut Set | Eight `M2.5x16` (or `M2.5x18`) + eight `M2.5x10` + six `M2.5x12` + six `M2.5x20` + sixteen `M2.5` nuts | [Amazon UK](https://www.amazon.co.uk/dp/B0FSWHZPGD) |
| `5 GBP` | `~1M` UHMWPE/Dyneema Cord | The low-friction high-strength cord for the pulleys (`1.6~2.0MM` Diameter) | (any by-the-metre seller; eBay, etc) |
| `20 GBP` | `15V` `90W` DC Power Supply | The power supply for the board and motors (standard `5.5x2.5MM` centre-positive barrel plug) | [Amazon UK](https://www.amazon.co.uk/dp/B09RHC7QG9) |
| `25 GBP` | 4/5/6-Point `2"` Harness | A low-cost Aliexpress model or used/expired FIA harness | [AliExpress](https://www.aliexpress.com/item/1005008051519590.html) |

> 📢 **Important:**
> - The `DDSM115` and `M0601` motors are the same OEM motor, but rebranded versions
> - The motors are _sometimes_ sold in **pairs**. Make sure you're only buying _two motors_, not _two sets of two_
> - There are multiple motor models in the `DDSMXXX` series. Make sure you're buying the [DDSM115](https://www.waveshare.com/wiki/DDSM115)
> - There are multiple control board models of similar appearance. Make sure you're buying the [DDSM Driver HAT (A)](https://www.waveshare.com/wiki/DDSM_Driver_HAT_(A)) (irrespective of which brand of motor you buy)
> - If using the _tubular_ motor brackets, you'll need [M5x25mm Clamping Knobs](https://www.amazon.co.uk/dp/B0CP2GQLQJ) and [M5 Nuts (8mm Hex)](https://www.amazon.co.uk/dp/B0FMRFPWJ3) to secure them to the tubing
> - `15V` is the currently recommended voltage, but some builders are using `19V` (commonly offered by laptop supplies)

### Belt Rollers

These are considered to be _optional_, but are usually required for seats with angled or irregularly shaped belt guides. They cost little to build, so are _recommended_ if you have any doubts about your seat's belt guide design or want maximum performance.

| Guide Price | Part | Description | Example |
| - | - | - | - |
| `5 GBP` | 4 x `605` Bearings | `5x14x5mm` bearings for the rollers | [Amazon UK](https://www.amazon.co.uk/dp/B0CZ8DJ6YM) / [Amazon UK](https://www.amazon.co.uk/dp/B0F6LNSC75) |
| `5 GBP` | 8 x `M5` Fully-Threaded Countersunk Bolts | Length depends on seat belt guide depth | [Amazon UK](https://www.amazon.co.uk/dp/B0C97LXKBP) |
| `5 GBP` | 8 x `M5` Hex Nuts (`8mm` WAF) | Must be `<5mm` thick | [Amazon UK](https://www.amazon.co.uk/dp/B0FMRFPWJ3) |

> 📢 **Important:**
> - Countersunk bolts are typically measured by their _entire length_ including the head
> - Measure your seat's belt guide/hole depth and _add_ `10mm`, rounding up to the nearest standard bolt length (e.g. my `39mm` belt guides need `50mm` bolts)
> - The bolts _must_ be fully threaded; otherwise you won't be able to use them for the roller axles
> - If you use bolts that are longer than needed, they may interfere with the belts and rollers

If _not_ using rollers, you can reduce friction (and wear) on your seat's belt loops if you apply some low-friction tape over the contact points. I've had success with [2-3/8" PTFE Tape](https://www.amazon.co.uk/dp/B0F3XKJW2V).

### Back-Driving Protection

You are _strongly encouraged_ to assemble and use this, as without it any rapid pulling on the belts may trigger the OVP/OCP within your power supply (as the motors act as _generators_ in this scenario), disabling tensioner functionality until time passes or a manual power supply reset is performed. There are a number of protection options detailed below. The [printable case](Printables/Back-Driving%20Protection%20Case) is designed to accommodate all of these.

> ⚡ **Warning:** All of these options add a modest capacitance between the power supply and controller board. If you disconnect the protection unit, the capacitor may remain charged at your supply voltage for a period of time. Do not touch or short the terminals at either end of the unit, as doing so **may cause a shock or damage equipment**.

The parts required will depend on your chosen option, but none should exceed `15 GBP` in cost:
- [Solderless + Ideal Diode](#solderless--ideal-diode): Using an ideal diode module with pre-soldered terminals
- [Soldered + Ideal Diode](#soldered--ideal-diode): Using an ideal diode module without terminals (requires soldering)
- [Discrete Schottky Diode](#discrete-schottky-diode): Using a discrete Schottky diode (requires _trickier_ soldering)

Back Driving Protection Options

#### Solderless + Ideal Diode

If you're at all uncomfortable with the idea of soldering or don't have the equipment, you can choose this option. You will need to cut and strip some wires, but no soldering is required.

We leverage the availability of premade 'Ideal Diode' modules with easy-to-use screw terminals and cheat a little by adding our capacitor across the output terminal, avoiding the need for any soldering at all.

| Guide Price | Part | Description | Example |
| - | - | - | - |
| `5 GBP` | Ideal Diode Module | A pre-made diode board with soldered screw terminals | [AliExpress](https://www.aliexpress.com/item/1005009419896467.html) |
| `5 GBP` | Capacitor | A `2200uF` `35V` electrolytic capacitor (just one; you'll have spares) | [Amazon UK](https://www.amazon.co.uk/dp/B07K87YFP9) |
| `5 GBP` | DC Cable | A `5.5x2.5mm` DC barrel plug to `XT60` adapter cable (or barrel-to-barrel extension)  | [Amazon UK](https://www.amazon.co.uk/dp/B0BPKNG672) or [Amazon UK](https://www.amazon.co.uk/dp/B0FJ8BKQCF) |

> 📢 **Important:** The printable case for the protection unit is intended for cables with a `5~5.5mm` external diameter, which is fairly typical. Any larger and you'll struggle to fit the cable into the ends of the case. Note also that the screw terminals on the diode board have a maximum gauge of roughly `10 AWG` (or `2.6mm` core diameter); though yours may vary.

The assembly instructions for this solderless option are included below under the [Assembly](#assembly) section.

#### Soldered + Ideal Diode

Soldered Option

This is essentially the same as the [Solderless + Ideal Diode](#solderless--ideal-diode) option; just using a premade 'Ideal Diode' module _without_ presoldered screw terimnals and soldering our wires and capacitor directly to the pads on the board.

As soldering jobs go this is very easy, and opens up many more options when it comes to 'Ideal Diode' modules. The one suggested for the solderless option can also be ordered without terminals and is a known good option; but you are not restricted to that specific module.

The main things you need to ensure of your chosen 'Ideal Diode' module are:
- The module actually blocks reverse current; not all such modules do (for 'OR-ing' purposes)
- The current handling exceeds `6A`
- The voltage handling exceeds `24V` (ideally `30V+`)
- The board has both `V+` and `GND` solder pads to make assembly easier (some omit the `GND` pads)

As long as these requirements are met, the module _should_ do the trick. These are some (unverified) examples:
- [Pololu 5382](https://www.pololu.com/product/5382)
- [Pololu 5383](https://www.pololu.com/product/5383)
- [Pololu 5388](https://www.pololu.com/product/5388)
- [Pololu 5389](https://www.pololu.com/product/5389)
- [Generic LM74700 Module](https://www.amazon.co.uk/dp/B0FNY9MWLX)
- [Generic 'Solar Diode' Module](https://www.amazon.co.uk/dp/B07QGW5J1H)

If you try any of these out or find others that work, please let me know and I'll add them to the list.

#### Discrete Schottky Diode

If you're a maker and familiar with electronics, a very simple circuit can be made using the same capacitor and any Schottky-like (e.g. SBR, SiC) diode with sufficient ratings. See above for the suggested values.

Strictly speaking this would be a downgrade from the 'Ideal Diode' style boards, but will still do the job just fine. Voltage drop is unlikely to be problematic with that class of diode, and the motors are wide-input.

See the diagrams above for a reference circuit design.

## Assembly

Depending on your choices above, some of these assembly instructions may not be relevant to you. Please read through the instructions and only follow the steps that are applicable to your build.

The photographs provided are for illustrative purposes and may not show the absolute latest part designs; don't worry if they aren't _exactly_ the same as the parts you've printed.

### Motors

| Step | Instructions | Illustration |
| :-: | :- | :-: |
| 1 | Since the motors are technically _wheels_, they come pre-fitted with rubber treads, which we need to remove.<br /><br />Unscrew the three `M2.5` bolts holding on motor face plate and remove it. You may need to remove a 'QA' sticker covering one of the screws.<br /><br />With the face plate removed, push the motor face (with the triangular hub) firmly with your thumbs, while holding the opposing face/rim of the tire with your fingers. Gradually working your way around the rim, moving small amounts at a time works best. | Wheel Motor |
| 2 | You'll be left with the bare motor. Keep the rubber tire, face plate and bolts safe though; in case you need to return the motors or repurpose them later. | Motor Without Tire |

### Pulleys

| Step | Instructions | Illustration |
| :-: | :- | :-: |
| 1 | Gather the four pulley parts; the bearing, the outer cover, the face plate and hub. | Pulley Parts |
| 2 | Press the bearing into the outer cover. This should be possible by hand. The accuracy/roughness of your print will dictate how easy this is.<br /><br />If the fit is too tight, use a hammer to _gently_ tap it in (alternating sides with each tap) or consider shaving away some material with a knife or file.<br /><br />If the fit is too loose, cut up a drinks can and shim around the edges of the bearing to fill in the gap (ensuring the shims do not protrude). | Inserting The BearingInserted Bearing |
| 3 | Insert the pulley face from the front so it sits inside the inner ring of the bearing. The notes above regarding fitting tolerances apply here too. | Face Inserted |
| 4 | Insert the pulley hub over the top, so that the triangular shape on the face part pushes into the triangular hole of the hub. They may pop together or be loose depending on the tolerances of your print (either is fine). The slot in the hub for the cord should be facing outward. | Hub Fitted |
| 6 | Cut a `0.5M` length of the _UHMWPE/Dyneema cord_ and tie a tight knot in the end, then remove any excess cord after the knot. | Knotting The Cord |
| 5 | Thread one end of the cord through one of the pulley cover holes. When assembling the _Left_ pulley, use the hole marked with `L` inside the pulley cover (or `R` for the _Right_ pulley). Push the knot into the cut-out in the pulley hub. It should stay in place relatively well. | Cord Inserted |
| 8 | Install the pulley onto the motor hub and insert and tighten three `M2.5x12MM` screws into the face plate. Make sure that the cord stays in the cut-out when doing so. | Installing The Pulley |

### Belt Clamps

| Step | Instructions | Illustration |
| :-: | --- | :-: |
| 1 | Gather the belt clamp parts; the four `M2.5x10` bolts, four `M2.5` nuts, and the front and rear plates. | Belt Clamp Parts |
| 1 | Insert `M2.5` nuts into the hexagonal holes on the underside of the rear clamp plate (as deeply as they will go). | Nuits Fitted |
| 2 | Tie a tight knot in other end of the cord you previously attached to the _Pulley_. Push the knot into the cut-out in the rear clamp plate, so the cord comes out the bottom. | Cord Fitted |
| 3 | Place the end of the harness belt into the rectangular detent of the rear clamp plate (it may overlap the knot; that's fine). Push the front clamp plate firmly down over both. | Belt PositionedClamp Applied |
| 4 | Keep pressure on the assembly while securing with the four `M2.5x10` bolts. Tighen each bolt partially in a circular pattern until they are all tight, rather than trying to fully tighten one at a time. | Tightening The Clamp |
| 5 | Once fully tightened, the two clamp parts should be fully touching with no visible gap between them. | Clamp TightenedClamp Fully Assembled |

### Brackets

| Step | Instructions | Illustration |
| :-: | --- | :-: |
| 1 | Gather the bracket parts; three `M2.5x20` bolts, the bracket and the motor (with or without pulley fitted). Since there are a number of bracket designs, the hardware needed to actually attach them to your rig will vary (but should be obvious if you already have a rig). | Bracket Parts |
| 1 | _Carefully_ feed the motor connectors and wires through the hole in the bracket. Bend back the smaller connector so you're not trying to push both through at once. | Folding Back The ConnectorWires Fed Through |
| 3 | Insert the motor stem into the socket on the braket. The shaft and socket are three-sided and symmetrical, so rotate it until it aligns with the socket and push in. As long as it sits fully into the socket, the angle doesn't matter. | Inserted The Motor |
| 2 | Secure the motor with the three `M2.5x20MM` bolts | Motor Bolted In |
| 3 | Attach the bracket to your rig frame. If using the _aluminium profile_ bracket designs, secure the bracket to your rig frame with suitable t-nuts and bolts. If using the tubular mount (with truss clamp), insert the `M10` nut into the printed backet slot, then secure it to the truss clamp with the `M10x16` bolt. | Assembled Bracket |

### Controller Board

| Step | Instructions | Illustration |
| :-: | --- | :-: |
| 1 | Gather the control board parts; the four `M2.5x16` bolts, four `M2.5` nuts, and the upper and lower shells. | Controller Board Parts |
| 2 | Flip the switch on the control board to the `USB` setting. | Switch Set To 'USB' |
| 3 | Insert `M2.5` nuts into the hexangonal holes on the underside of the lower printed case (as deeply as they will go). | Nuts Inserted |
| 4 | Insert the board into the lower half of the printed case. The _Raspberry Pi_ header on the rear may be a tight fit here; push down on the white circles either side of the header to press this in. | Board Inserted |
| 5 | Place the upper half of the case on top and secure with four `M2.5x16` bolts. | Case Assembled |

### Belt Rollers

| Step | Instructions | Illustration |
| :-: | --- | :-: |
| 1 | Gather the parts for each belt roller; the five `M5` bolts (length according to your belt guide depth), five `M5` nuts, three spacers, two `605` bearings, bracket, plate and roller. | Belt Roller Parts |
| 2 | Press-fit the bearings into the ends of the roller. | Fitting The Bearings |
| 3 | Insert two `M5` nuts into the inside faces of the bracket ends and thread in the `M5` bolts from the outside; no more than a couple turns (so their ends are flush with the nuts). | Inserting Nuts & Bolts |
| 4 | Position the roller between the bracket ends and start screwing in the bolts all the way, securing the roller in place. | Attaching The Roller |
| 5 | Take the partially assembled roller and remaining parts to your sim rig. | Partially Assembled |
| 6 | Establish where you'd like to mount the roller and which positioning holes you'll use. The roller must be as close to horizontal as possible and nideally cover the entire width of the belt guide hole. Horizontal guides only require two holes/bolts, while angled guides typically require three to prevent sideways movement. | Positioning |
| 7 | On the face plate, find the corresponding holes to the ones you previously chose and insert the `M5` bolts. Place the printed spacers over those. | Bolts & Spacers |
| 8 | Position the face plate inside the belt guide, with the bolts resting on the bottom face of the belt guide hole. At this point you may need to feed through your belt, as there may not be space to do so once the roller is fitted. | Face Plate |
| 9 | Line up the bracket with the face plate and bolts, then insert the `M5` nuts and tighten from the other side. The face plate and bracket should _lightly_ clamp to the front and back faces of the seat's belt guide. | Bracket Installation |
| 10 | Repeat for the other side and if you haven't already, feed the belts through and check that everything is moving freely. | Installed |

The choice of which holes to use is up to you and very much specific to your seat design. Below are some placement examples for common seat belt guide shapes. Note that horizontal belt guides can be fitted with only two `M5` positioning bolts, while angled guides usually need three to prevent sideways movement:

Belt Guide Shapes

### Back-Driving Protection

| Step | Instructions | Illustration |
| :-: | :- | :-: |
| 1 | Assemble the protection unit parts; the four `M2.5x16` bolts, four `M2.5` nuts, the capacitor, the diode board, the adapter cable and printed case. Cut the adapter cable in half as shown. | The Protection Unit Parts |
| 2 | Bend the capacitor legs as pictured, taking care not to damage the capacitor and noting the oritentation shown. If the legs of the screw terminals protrude significantly from the bottom of the board, take this opportunity to trim them down with some snips. | Preparing The Capacitor |
| 3 | Fully loosen the screw terminals. Insert the capacitor legs into the **output** screw terminals as shown (`GND` and `VOUT` on the board). with the capacitor `-` leg going into the board's `GND` as pictured. Do not tighten the terminals yet. | Fitting The Capacitor |
| 4 | Trim off roughly `6mm` of sheathing from the adapter cable ends and twist as shown. |  |
| 6 | Insert the bare wires into the screw terminals. The `XT60` cable should be on the **output** side and the round DC barrel cable should be on the **input** side. **Black** to `GND` and **red** to `VOUT` and `VIN`. Tighten up the screws as much as they will go. |  Inserting The Wires |
| 5 | Check for any stray or loose wires and adjust if needed. Install the unit into the printed case, taking care not to disturb the fitted wires. Make sure that the black outer sheath of the cable goes _completely inside_ the case as shown, so that the case lid can clamp down on it once closed. | Fitting Into The Case |
| 8 | Install the `M2.5x16MM` screws and nuts into the case and tighten as much as they will reasonably go. Ideally if you happen to have a multimeter, before attempting to power the controller board, check that the `XT60` connector produces the expected `15V` in the correct polarity (the **flat** side should be `+` and the **beveled** side `-`) when the power supply is connected to the dc barrel plug. |  The Completed Protection Unit |

## Wiring Up

Since the Waveshare board and motors are plug-and play, this is pretty straight forward.

If you're using the [Back-Driving Protection](#back-driving-protection), plug that into the control board (either the XT60 or DC Barrel sockets) and then into the power supply; otherwise just plug the power supply into the board directly.

If this is your first-time setup, your motors will need to be configured, so start with only a single motor plugged into the board. The plugin will tell you when to plug in the second motor.

It doesn't matter which of the exposed connectors on the top of the board you use for each motor. Make sure you've fully seated both the two-pin power plug and four-pin data plug.

Plug your USB type-c cable (one is supplied with the board) into the USB socket closest to the power connectors (marked `DDSM` on the board). If you use the other USB socket, it won't work.

If everything is connected correctly, the board will be detected by the SimHub plugin. No drivers are required.

> ⚠️ **Important:** Do not attempt to power or test the motors while not securely installed on the rig. If they start rotating while loose, they'll move around and potentially destroy themselves, the control board and the surface they are on

## Adjustment

Pulley & USB Port Guidance (https://www.youtube.com/watch?v=9At6qqblOZY)

If you already have a harness, you'll be accustomed to tightening it up with the buckles/straps it has. **You don't need to do that with this tensioner**, since it pre-tensions the harness for you (see `Idle Tension` in the `Tension` tab of the plugin).

However when first setting up the tensioner, you'll need to ensure the following:
- There is enough _plain belt_ (with no buckles or wider sections) to slide through the belt holes on your seat unhindered (allow for at least `20CM` of movement)
- Any excess belt is tucked/buckled away such that it does not catch or rub on anything

If you have excess shoulder belt length, you should run it through the seat holes and then buckle it back upon itself behind the seat (just above where you apply the tensioner's cord clamps).

Belt Clamps

The method of adjustment may depend on your chosen belt clamp design:
- **End Clamps**: These require the shortening of the harness shoulder belts, which is _strongly discouraged_ until you're 100% happy with your setup. Try using the belt buckles that likely came with your harness to make non-destructive adjustments to length first
- **Through Clamps**: Loosen the clamp bolts and simply slide the clamp up or down the length of the harness shoulder belts, then retighten in the desired location
- **Loop Clamps**: You'll already be using belt buckles to secure the looped harness shoulder belts against themselves, so simply adjust those buckles until you achieve the desired lengths

Adjustment

For reference, a _single turn_ of the pulley is about `~10CM` of cord. This is useful when working out how much cord you have wrapped around the enclosed pulley.

Since our harness is going to be self-adjusting (at least in the shoulders), we should make sure we have `~25CM` of cord between the belt clamps and the pulleys. Obviously we do not want our belt clamps colliding with the pulleys under normal operation.

We also want there to _always_ be at least some cord wrapped around the pulleys (`10~20CM`), as the motors will be unable to apply torque properly if the cord is fully unwound. Do not wrap more than `40CM` or about _four turns_ of cord, as this will start to bind the pulley.

Cord Wrapping

It is important that the cord is aligned such that it does not rub against the _sides_ of the pulley housing. The housing is designed to freely rotate with the cord at any angle along the axis of the motor; so if you move your chair backwards or forwards, it doesn't cause a problem. However the motor pulleys must line up perfectly underneath the seat's belt holes to avoid rubbing. In other words, the motor axles must be _perpendicular_ to the cords:

Pulley Alignment

_(Instructional Video TBC)_

## Software

See the [/Software/](/Software/) directory for the _SimHub_ plugin download and installation instructions.

## Troubleshooting

See the [FAQ.md](FAQ.md) document for common issues and their solutions. If you have any questions or need further assistance, please reach out via [a new discussion](/discussions/new/choose) or [create a new issue](/issues/new) describing your problem or request.

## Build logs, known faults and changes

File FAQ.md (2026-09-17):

# Frequently Asked Questions

Naturally potential **SABT** builders have questions about the kit before committing to a build.

Builders also have technical questions about the setup and operation of the kit, or may encounter issues during assembly or use.

- [General Pre-Build Queries](#general-pre-build-queries)
    - [How long does it take to build the kit?](#how-long-does-it-take-to-build-the-kit)
    - [How does it perform compared to other belt tensioners?](#how-does-it-perform-compared-to-other-belt-tensioners)
    - [What is the latency like?](#what-is-the-latency-like)
    - [How long will it last?](#how-long-will-it-last)
    - [Who are you and what is your background?](#who-are-you-and-what-is-your-background)
- [Component Selection](#component-selection)
    - [Can I use a different type of motor?](#can-i-use-a-different-type-of-motor)
    - [Can I use a different control board?](#can-i-use-a-different-control-board)
    - [Can I use higher voltages?](#can-i-use-higher-voltages)
    - [What ype of harness do I need?](#what-type-of-harness-do-i-need)
- [Assembly & Adjustment](#assembly--adjustment)
    - [My pulley covers are not spinning freely](#my-pulley-covers-are-not-spinning-freely)
    - [The cords are tangling up when not under tension](#the-cords-are-tangling-up-when-not-under-tension)
    - [The cords or belts are rubbing against the back of my seat](#the-cords-or-belts-are-rubbing-against-the-back-of-my-seat)
- [Setup & Connectivity](#setup--connectivity)
    - [Why are there two USB ports on the control board?](#why-are-there-two-usb-ports-on-the-control-board)
    - [Which USB port should I use?](#which-usb-port-should-i-use)
    - [Which power connector should I use?](#which-power-connector-should-i-use)
    - [Which position should the switch on the control board be in?](#which-position-should-the-switch-on-the-control-board-be-in)
    - [Which serial/COM port should I select in the SimHub plugin?](#which-serial-or-com-port-should-i-select-in-the-simhub-plugin)
    - [Why are the motors not being detected by the plugin?](#why-are-the-motors-not-being-detected-by-the-plugin)
    - [Can I control the tensioner with buttons?](#can-i-control-the-tensioner-with-buttons)
- [Performance & Effects](#performance--effects)
    - [I'm not getting much force from the belts](#im-not-getting-much-force-from-the-belts)
    - [Force effects seem to be sluggish or muted](#force-effects-seem-to-be-sluggish-or-muted)
    - [Are flight sims supported?](#are-flight-sims-supported)
    - [Why can't I feel engine vibrations or kerb hits?](#why-cant-i-feel-engine-vibrations-or-kerb-hits)

These are common and anticipated questions and their answers. If you have a question that isn't answered here, please reach out via [a new discussion](/discussions/new/choose) or [create a new issue](/issues/new) describing your problem or request.

## General Pre-Build Queries

### How long does it take to build the kit?

Printing the parts can take several hours, depending on your printer and chosen options.

The assembly and setup **shouldn't take more than an afternoon**; though all sim rigs are different and you _may_ run into unique challenges that you'll need to solve.

SABT was designed with non-technical builders in mind, so the parts count was deliberately kept low and the assembly process is straightforward.

The SimHub plugin takes care of all of the software, and is simply copy+pasted into your SimHub installation folder.

### How does it perform compared to other belt tensioners?

**SABT** is a _force-based_ system which directly maps telemetry forces to output, so should provide a more realistic experience than _position/angle-based_ systems.

It is also _direct-drive_, so operates silently and smoothly. This permits it to act with a 'spring' effect and auto-tension the belts, meaning you don't have to pre-tighten your harness.

The maximum force output of **SABT** is roughly 10Kg per belt. This is roughly half that of the [QS BT-1](https://qubicsystem.com/product/qs-bt1).

Some other DIY options offer considerably more power; particularly those using larger geared NEMA-format motors.

Remember that **SABT** is designed to be _low-cost_ and _easy-to-build_. It is not intended to compete with high-end options costing many times more. If you are seeking maximum performance, you should consider other options.

### What is the latency like?

Testing this accurately requires equipment I do not have; but I _have_ created a simple [demonstration video](https://youtube.com/shorts/pNn5PLNhad8) that uses the audible 'clack' of my shifter paddles to illustrate how quickly the motors respond to the change in acceleration caused by the gear-change.

The video shows this taking _roughly_ two frames at 60fps, which equates to `33ms`.

However that period is measured from the very start of the audible 'clack' waveform, which is some time _before_ the input is sent to the game and the resulting telemetry is made available by SimHub. Therefore the actual latency will be lower than that.

Total latency will vary depending on the game and your particular system.

The minimum achievable latency is constrained by _SimHub's_ telemetry update rate. For the (required) _licensed version_ this is `60Hz` (or `16.6ms`).

### How long will it last?

At the time of writing the project has only been public a few months, so long-term reliability is unknown. The **SABT** SimHub plugin _does not_ track usage, so I have no idea how heavily it is being used by the community.

There are at least **thirty** builds in the wild and I have yet to receive reports of any motor or controller failures. We are theoretically using them within their rated specifications, but probably not in the intended manner.

Motor or controller failures _may_ potentially be covered under your retailer's returns policy or manufacturer's warranty; but I would not rely on that being the case. Obviously as an open-source project, the authors provide absolutely no warranty, guarantees, compensation or responsibility for failed parts.

Assume that you may lose your investment; if that is not acceptable to you, I suggest paying a much higher price up-front for a commercial turnkey product with a full warranty and support.

### Who are you and what is your background?

My name is _George Wilkins_. I'm located in the United Kingdom and have been a professional software developer (web technology) for 20 years. One of my interests is hobby engineering and I'm always working on multiple projects across various disciplines. I recently got back into sim racing (after a couple decades away) and  noticed a few gaps in the peripherals market while building [my own rig](https://photos.app.goo.gl/Egvd6EPmVJsZK7Hn9).

I developed the [BDH Active Shifter](https://bdhracesim.com/uk/products/active/), which started off as a modification of the [BDH H1](https://bdhracesim.com/uk/products/h1/) and turned into a formal collaboration with BDH.

Towards the end of that project I started independently developing **SABT**, with the goal of making _active belt tensioning_ more accessible to the sim racing community.

## Component Selection

### Can I use a different type of motor?

The BOM states the [Waveshare DDSM115](https://www.waveshare.com/wiki/DDSM115) or [DFRobot M0601](https://www.dfrobot.com/product-3077.html) motors should be used. These are both rebranded versions of the same [Direct Drive Tech](https://shop.directdrive.com) motor, which appears to be designated the [M0601C-111](https://shop.directdrive.com/products/m0601c-111-direct-drive-motor).

I developed the **SABT** kit using the `DDSM115`. Other builders have since reported success with the `M0601`. There may be other rebrands of the same motor available, but they have not been tested. If you find one; let me know.

As for other types of motors; the printed parts, electronics and SimHub plugin are designed to work _only_ with the two motors noted above. You would have to modify or replace _all_ of these to make the tensioner work with other motor hardware.

If there is demand, a version of the kit for more powerful motors could be developed; but you'd lose the plug-and-play nature of the current design, requiring a custom PCB to control them.

### Can I use a different control board?

It would be possible to control the DDSM115 motors with a generic RS485-USB adapter board. In fact, that's one of the approaches I considered when designing the kit. However you'd need two of those adapters to run the motors separately (or add custom electonics to support both motors on a single adapter), and the SimHub plugin would need to be modified to support the different control hardware.

Generally it would be more expensive and complicated than just using the Waveshare control board.

If the project becomes particularly popular there's a good chance I'll look at designing and manufacturing a custom board that integrates everything we need (including the back-driving protection circuitry), but for now the Waveshare board is a good off-the-shelf solution.

### Can I use higher voltages?

The recommended `15V` was chosen to protect your motors. I would strongly suggest no more than `19V`.

The motors are _"wide-input"_, meaning they will accept a variety of input voltages between `12V` and `24V`. The _"rated voltage"_ is given as `18V` and `5S LiPo`, because as part of a robotics platform, they're intended to be powered by a battery pack. The control board simply passes the supply voltage through to the motors, so the motors will run at whatever voltage you supply to the board.

Since we're running from an SMPS, we have to pick from the commonly available voltages (e.g. `12V`, `15V`, `19V` or `24V`). Higher voltages for these _FOC_ servo motors result in a more energetic response, but not more torque. In practice, SABT builders have also reported higher operating temperatures at higher voltages.

An additional consideration is _back-driving_ of the motors. This is a situation where the motors are turned by the belts (for example, by you moving forward in your seat, or pulling the belts over your shoulder to fit your harness). The motors convert that mechanical movement into electrical energy, which must be dissipated somewhere (manifesting as a voltage spike).

In a battery-driven application, this is not a problem as the battery can absorb the energy (in effect, _regenerative braking_). In our SMPS-driven setup, without any extra protection circuitry this will typically trigger the OVP/RC features of the power supply. The [back-driving protection unit](INSTRUCTIONS.md#back-driving-protection) was devised to prevent this from happening. However it doesn't _stop_ the voltage spike; it simply blocks it from returning to the supply and instead dumps it into a capacitor. Once the voltage spike has been absorbed and the external mechanical input ceased, the motors draw this back down to the supply voltage and continue as normal.

Running your motors at a higher voltage means any relative spike that occurs will also be higher; potentially exceeding the voltage limits of the motors. This is why I would never run my motors at the maximum `24V` and chose `15V` as a recommended safe operating voltage.

However there is an argument to be made for running at `19V`. This is a _very common_ voltage for laptop power supplies; which means many highy-quality supplies are available for virtually nothing. You probably already have at least one in your home from an old device. A number of SABT builders have reported good results running at `19V`, but this is typically joined by higher operating temperatures. While there are temperature-throttling features built into the plugin software, you may wish to look into active cooling of the motors if you intend to run at this voltage. You'll also want to use suitable filaments for the printed parts, such as PETG or ABS, which are more heat-resistant than PLA.

### What type of harness do I need?

Conventional wisdom with _active belt tensioners_ is that a five or six-point harness is required to prevent the belts from pulling _upwards_ rather than _into_ your body, with the 'anti-submarine' belt(s) anchoring the harness into the lap (rather than serving as a safety feature in a real vehicle). This is certainly a more realistic setup for simulating race-specification vehicles, but obviously overkill road vehicles that would be fitted with inertia-reel seatbelts.

A number of builders have reported good performance with four-point configurations; specifically 'backpack' style setups where the shoulder straps are anchored directly to the sides of the seat, with nothing connecting each side and no anti-submarine belt. This has been reported to actually enhance the tensioning effects while reducing the hassle and discomfort of a five or six-point harness.

Regardless of your chosen harness configuration, a `2"` (`50mm`) belt width is recommended; as this should pass through all seat belt guide holes, minimises friction and can be accommodated by the project's included belt roller design.

## Assembly & Adjustment

### My pulley covers are not spinning freely

Most likely the bearings are not seated correctly in the pulley covers, or the end of the cord is not quite inside the slot/hole in the centre of the pulley and it's pushing the cover out of alignment. One way to check is to remove the cords and re-attach the covers to see if they spin freely without the cords in place. If they do, then the cords were being pinched somewhere inside the pulleys.

Reassemble the pulleys and make sure the cords are seated correctly in the pulley slots as pictured in the instructions. If the cord ends have frayed, consider trimming them back.

In rare cases, your printed pulley parts may be warped or undersized; in which case you will likely need to reprint them. I suggest [getting in touch](/discussions/new/choose) before doing so, as there may be a simple fix or adjustment that can be made to avoid reprinting.

### The cords are tangling up when not under tension

With some UHMWPE/Dyneema cords, it is quite easy to twist them during installation. If done excessively, the cords will try to return to their untwisted state when the tensioner is not under load, which can cause them to tangle up. Remove the cords from the pulleys, straighten them out and re-install them, taking care not to twist them during installation.

### The cords or belts are rubbing against the back of my seat

You'll need to print taller motor brackets or add a spacer between your existing brackets and your mounting surface.

Various designs are available in the [Printables](/Printables/Motor%20Brackets) directory.

## Setup & Connectivity

### Why are there two USB ports on the control board?

### Which USB port should I use?

The Waveshare control board has two USB ports, but only one of them is used for the **SABT** kit.

The port we use is essentially a direct connection to the motor drivers via a USB to RS485 adapter that's built into the Waveshare control board. It allows a host PC to send commands directly to the motor drivers.

The other port connects to an ESP32 microcontroller embedded on the control board, which also has access to the motor drivers and can be programmed to control the motors directly. That's what you'd use if working on a robotics project, which is what the control board is primarily designed for.

In our case the SimHub plugin does the telemetry and force calculations needed for our belt tensioning, so we don't need to use the ESP32 at all.

### Which power connector should I use?

There are two power connectors on the controller board; a `5.5x2.5mm` DC barrel jack and an `XT60` socket. They are electrically commoned together, so it makes no electrical difference which one you use.

It is most likely that you have a power supply with a DC barrel plug, so that is what you'll use. The `XT60` connector is a better choice otherwise, as it is less likely to come loose when exposed to vibration and movement. However if you make sure to zip-tie (or otherwise secure) the power cable close to the control board, neither connection should be a problem.

### Which position should the switch on the control board be in?

The small sliding switch near the centre of the control board is used to select whether the motors are controlled by the onboard ESP32 microcontroller or by the host computer (via the USB port). For our purposes, it should be set to the `USB` position; sliding it over to the position closest to the USB and power ports.

### Which serial or COM port should I select in the SimHub plugin?

The plugin will attempt to automatically identify and select your control board's serial port.

However you may find _multiple_ serial/COM ports listed in the SimHub plugin. If so, it means another device is using the same serial bridge chip as our control board. That's not a problem; just unplug the control board briefly to see which port disappears from the list, then plug it back in and select that port in the plugin when it reappears in the list.

### Why are the motors not being detected by the plugin?

Most connectivity problems happen while first setting up the motors. Once they're detected and configured, things should work reliably.

If the motors are not being detected or the guided setup process is failing, check the following:
- Check that you've used the correct USB port on the control board (the one closest to the power inputs)
- Check that the sliding switch on the control board is set to the `USB` position (the position closest to the USB and power ports)
- Check that the control board is powered with 15V~19V (and using the correct polarity)
- If using the back-driving protection unit, check that it is functioning correctly. Try without it to see if it's causing the problem
- Check that the motor connector(s) are properly seated on the controller board
- Try unplugging other USB devices (and disabling associated SimHub plugins) temporarily during the motor setup
- Restart your computer
- Check that _Device Manager_ can see a `USB-Enhanced-SERIAL CH343` device (under `Ports (COM & LPT)`) when the control board is connected
- If also using the _"Arduino"_ [feature](https://github.com/SHWotever/SimHub/wiki/Arduino--Setup) of _SimHub_, check that it is not trying to scan the SABT serial port (as this will block SABT from doing so); either adding an exception to its port scanning functionality (or disabling it entirely)

You can verify that the motors are powered by trying to turn them manually (by their shells, not the pulleys or cords). If they are powered, you should feel very noticable resistance. If they turn freely, the motors are not being powered.

### Can I control the tensioner with buttons?

Yes, SimHub has a `Controls & Events` feature that allows the mapping of any input device to any action exposed by a plugin; and the **SABT** plugin exposes various actions:
1. Select `Controls & Events` on the left-hand SimHub menu
2. Enter `sabt` into the `Target` filter to find the available actions
3. Select the desired action
4. Choose your input device and buttons under `Source`
5. Set the `Input Mode` to `ShortPress` or `LongPressNoAutoRepeat` (the latter is recommended if using the `...WithoutWarning` variations of actions)

> ⚠️ **Warning:**
> The `...WithoutWarning` variations of actions explicitly bypass any on-screen warnings related to powering-on the motors, so use with care.

## Performance & Effects

### I'm not getting much force from the belts

### Force effects seem to be sluggish or muted

Have a look at the [adjustment instructions](INSTRUCTIONS.md#adjustment) and then:
- Check that the cords are coming out of the pulleys at a perpendicular angle to the motor axles. They should not be touching the sides of the hole in the pulley (viewed from the side of the motor)
- When your harness is fitted and closed, there should be at least some cord wound around the pulleys. If not, the motors won't be able to apply torque to the belts as effectively as they could. Remember that this system is self-tightening, so you do not need to make your harness tight before closing it; the motors will do that for you
- Check if your cord or belts are snagging on anything; consider adding low-friction tape to your seat's belt holes to reduce belt friction or add the [Belt Rollers](INSTRUCTIONS.md#belt-rollers) for a smoother experience
- Re-tune the telemetry handling and effects settings for the game (and potentially specific vehicle class) in the SimHub plugin

### Are flight sims supported?

Strictly speaking _any_ games fully supported by SimHub are automatically supported by the SABT plugin, as it uses the normalised telemetry data from SimHub's API. However the plugin is primarily designed for sim racing (cars, trucks, etc). The UI and effects sliders are all designed with that in mind and flight-specific effects are not currently implemented.

This may change in a future release; but that will likely be a new major version with a sigificant rework of the plugin's UI and effects handling. If you are interested in this, please [add your voice](https://github.com/GeorgeWilkins/Simple-Active-Belt-Tensioner/issues/38) to the existing issue regarding this functionality. The more interest there is, the higher priority it will be given.

### Why can't I feel engine vibrations or kerb hits?

The tensioner is designed to simulate sustained forces such as braking, acceleration and cornering. It can also simulate large impactful _heave_ events (such as jumps or dips). However it is not intended to simulate high-frequency vibrations or small bumps. That is the job of tactile transducers (or "bass shakers") which are designed specifically to create those effects.

Adjusting the tensioner to express these small/brief impacts effects _is possible_, but it makes all other output extremely aggressive and overly sensitive. All braking, acceleration and cornering forces become oversaturated, making for an unpleasant experience.

There is [a feature request](https://github.com/GeorgeWilkins/Simple-Active-Belt-Tensioner/issues/74) being worked on that adds some additional effects (such as engine vibrations) to the plugin; however these are not strictly force-based (instead using RPM telemetry to achieve an _approximation_ of engine vibration) and will not be as realistic as a dedicated tactile transducer.

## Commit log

2026-03-02 Switching to CERN license
2026-03-15 Adding assembly instructions & images
2026-03-15 Adding more assembly process images
2026-03-22 Updating pulley imagery for latest design
2026-03-22 Adding Printables
    [Belt Clamp Front.step, Belt Clamp Rear.step, Belt Clamp.FCStd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]
2026-03-22 Renaming files
    [Corner Bracket (30~40MM Profile).FCStd, Flat Bracket (30~40MM Profile).FCStd]
2026-03-22 Correcting file name
    [Pulley (6706 Bearing).FCStd]
2026-03-23 Adding tube clamp brackets
    [Truss Clamp Bracket (50MM Tube).FCStd, Truss Clamp Bracket (50MM Tube).step]
2026-03-29 Adding Initial Plugin DLL, Removing Branded Files
    [Belt Clamp Front.step, Belt Clamp Rear.step, Controller Case Base.step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]
2026-03-29 Adding Printables, Rearranging & Renaming, Adding Notes
    [6706 Bearing Pulley (Cover).step, 6706 Bearing Pulley (Face).step, 6706 Bearing Pulley (Hub).step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]
2026-04-05 Adding Plugin Source, Amending Printables
    [6706 Bearing Pulley.FCStd, 6809 Bearing Pulley (Cover).step, 6809 Bearing Pulley (Face).step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]
2026-04-05 Correcting Links, Removing Alternate Pulley Size References
2026-04-05 Updating power supply information
2026-04-09 Major refactoring of motor logic & UI handling
2026-04-11 Correcting Test Torque Direction
2026-04-11 Reversing Test Torque
2026-04-13 Adding back-driving protection case & MJF results
2026-04-13 Renaming printable files
    [Back-Driving Protection Case (Base).step, Back-Driving Protection Case (Top).step]
2026-04-25 Adding note regarding belt rollers
2026-04-25 Adding note regarding powering off
2026-04-26 Adding power supply protection unit instructions
2026-04-26 Updating protection unit case
    [Back-Driving Protection Case (Base).step, Back-Driving Protection Case (Top).step, Back-Driving Protection Case.FCStd]
2026-04-26 Adding soldered protection board image, software link
    Updated instructions for hardware assembly and software reference.
2026-04-26 Adjusting controller case for board tolerances
    [Controller Case (Top).step, Controller Case.FCStd]
2026-04-27 Correcting opening alignment, removing old designs
    [Back-Driving Protection Case (Generic LM74700 or XL0401).FCStd, Controller Case (Tall).FCStd, Controller Case (Top).step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]
2026-04-27 Amending motor configuration process, reworking status UI and handling
2026-04-27 Adding notes on pulley alignment
2026-04-27 Updating source file references, adding 'SABT' branding note
    [Pulley.FCStd]
2026-04-28 Updating bolt counts for protection unit case
2026-06-11 Implementing Temperature Reading & Output
2026-06-25 Implementing motor direction reverse toggle
